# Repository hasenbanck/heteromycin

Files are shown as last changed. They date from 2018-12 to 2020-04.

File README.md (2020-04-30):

# Heteromycin - 3D printer board

Heteromycin is a 3D printer controller that aims to provide a full stack user
experience around Octoprint / Marlin using a custom designed board that
integrates a Raspberry Pi 3 or Zero W. It will also provide a solid, powerfull
hardware by utilizing quality components, a STM32 32bit MCU and powerfull
TMC5160 or TMC2160 driver (SD / SPI mode).

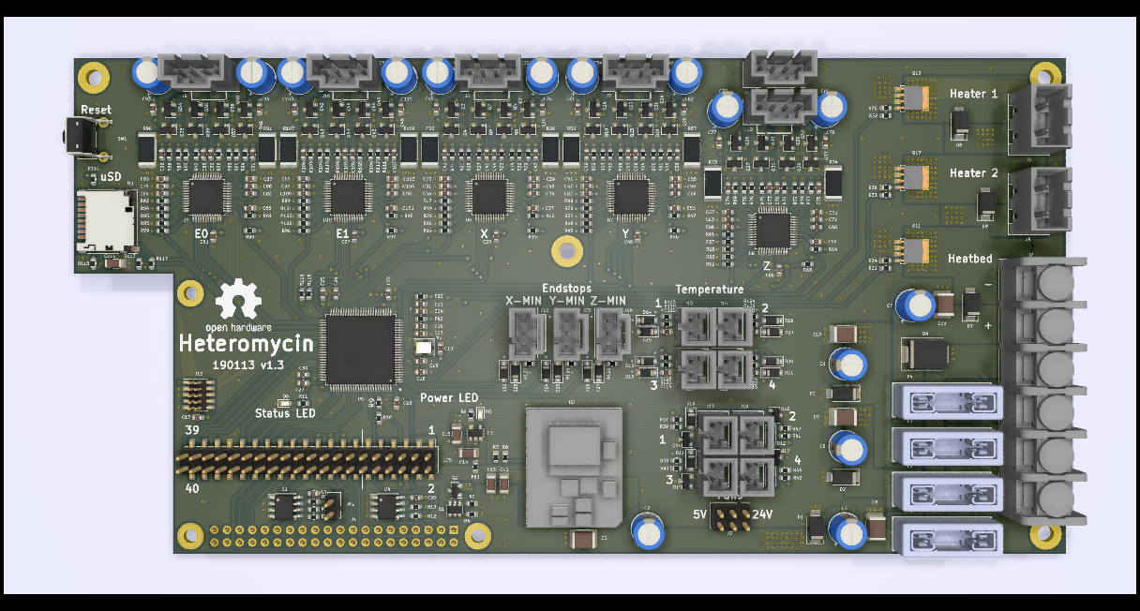
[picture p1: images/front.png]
heteromycin version 1.0


## Features

* 32bit STM32H743VI 400Mhz / 1024KiB RAM / 2MiB Flash MCU / 4 KiB EEPROM
* Integrated Raspberry Pi 3 / Zero W HAT connector as the main user interface
* Integrated DC/DC switching module for 5V / 3.3V power supply
* 5x TMC5160 or TMC2160 stepper driver with 8x external Power MOSFET each
* 3x high power MOSFET for heating (2x heater, 1x heatbed, 24V)
* 4x low power MOSFET for fans (5V or 24V)
* 40 pin external connector for STM32 and Pi GPIO pins
  * GPIO
  * PWM
  * UART
  * SPI
  * I2C
  * 3.3V / 5V / GND for external power consumption
* Micro SD Card for storing GCODE files (directa MCU access)
* Designed for a 24V power supply
* Automotive fuses
* Quality connectors
* Octoprint plugin for flashing the firmware of the board (STM32)

## Roadmap

* Hardware
  * [x] Describe the general functionality and select the main components
  * [x] Draw the schematics of the PCB
  * [x] Placement & routing of the PCB
  * [ ] Production of a development board
  * [ ] Testing the PCB
  * [ ] Repreat until hardware is finished
* Software
  * [x] Write arduino core board definition once first PCB design is finished
  * [ ] Write PIN file for Marlin
  * [ ] Test board (esp. the TMC*160 driver)
  * [ ] Octoprint plugin for firmware upgrade
  * [ ] STM32flash rewrite (fix I2C and add SPI, maybe rewrite in rust)
  * [ ] Create a script / image with Octoprint with the plugin / tools
  preinstalled
  * [ ] Documentation

## Alternative Parts

### Stepper driver

You can use both TMC5160 or TMC2160 as the stepper driver, since they both are
functionally / pin equal when used in SD / SPI-Mode.

It doesn't mater choosing one over the other, other than price and availability.

Fine tuning of the MOSFET driver may be necessary.

## License

The hardware is licensed under CERN OHL version 1.2.
The software is licensed under GNU GPL v3.

The files under PCB/packages3d are excluded from this license and are provided
under fair use terms for this open-source project.

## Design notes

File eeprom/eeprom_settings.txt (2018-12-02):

########################################################################
# EEPROM settings text file
#
# Edit this file for your particular board and run through eepmake tool,
# then use eepflash tool to write to attached HAT ID EEPROM
#
# Tools available:
#  eepmake   Parses EEPROM text file and creates binary .eep file
#  eepdump   Dumps a binary .eep file as human readable text (for debug)
#  eepflash  Write or read .eep binary image to/from HAT EEPROM
#
########################################################################

########################################################################
# Vendor info

# 128 bit UUID. If left at zero eepmake tool will auto-generate
# RFC 4122 compliant UUID
product_uuid ba184594-9e9b-4886-a79a-3c380cfe95e4

# 16 bit product id
product_id 0xFE10

# 16 bit product version
product_ver 0x0001

# ASCII vendor string  (max 255 characters)
vendor "Heteromycin development team"

# ASCII product string (max 255 characters)
product "3D printer controller Heteromycin"

########################################################################
# GPIO bank settings, set to nonzero to change from the default.
# NOTE these setting can only be set per BANK, uncommenting any of
# these will force the bank to use the custom setting.

# drive strength, 0=default, 1-8=2,4,6,8,10,12,14,16mA, 9-15=reserved
gpio_drive 0

# 0=default, 1=slew rate limiting, 2=no slew limiting, 3=reserved
gpio_slew 0

# 0=default, 1=hysteresis disabled, 2=hysteresis enabled, 3=reserved
gpio_hysteresis 0

# If board back-powers Pi via 5V GPIO header pins:
# 0 = board does not back-power
# 1 = board back-powers and can supply the Pi with a minimum of 1.3A
# 2 = board back-powers and can supply the Pi with a minimum of 2A
# 3 = reserved
# If back_power=2 then USB high current mode will be automatically
# enabled on the Pi
back_power 2 # Heteromycin can provide up to 8A on the 5V rail

########################################################################
# GPIO pins, uncomment for GPIOs used on board
# Options for FUNCTION: INPUT, OUTPUT, ALT0-ALT5
# Options for PULL: DEFAULT, UP, DOWN, NONE
# NB GPIO0 and GPIO1 are reserved for ID EEPROM so cannot be set

#         GPIO  FUNCTION  PULL
#         ----  --------  ----

#####
# We define GPIO pins at startup as INPUTS and user programms can later
# define the needed behavior, this way we boot in a known state and don't
# cause any unforseen resets or problems.
#####

setgpio  2     ALT0     DEFAULT # SDA
setgpio  3     ALT0     DEFAULT # SCL
setgpio  4     INPUT    NONE    # MCU BOOT Pin
setgpio  5     INPUT    NONE # GPIO
setgpio  6     INPUT    NONE # GPIO
setgpio  7     ALT0     DEFAULT # SS_0
setgpio  8     ALT0     DEFAULT # SS_1
setgpio  9     ALT0     DEFAULT # MISO
setgpio  10    ALT0     DEFAULT # MOSI
setgpio  11    ALT0     DEFAULT # SCLK
#setgpio  12    INPUT     DEFAULT
setgpio  13    INPUT    DEFAULT # GPIO
setgpio  14    ALT0     DEFAULT # TX
setgpio  15    ALT0     DEFAULT # RX
#setgpio  16    INPUT     DEFAULT
#setgpio  17    INPUT     DEFAULT
setgpio  18    INPUT    NONE # MCU nRESET Pin
setgpio  19    INPUT    NONE # GPIO
#setgpio  20    INPUT     DEFAULT
#setgpio  21    INPUT     DEFAULT
#setgpio  22    INPUT     DEFAULT
#setgpio  23    INPUT     DEFAULT
#setgpio  24    INPUT     DEFAULT
#setgpio  25    INPUT     DEFAULT
#setgpio  26    INPUT     DEFAULT
#setgpio  27    INPUT     DEFAULT

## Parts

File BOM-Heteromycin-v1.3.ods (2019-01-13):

Reference(s) | Value | Mft. Nr. | Digikey Nr. | Mouser Nr. | LCSC Nr. | Qty | Footprint | Note | Datasheet
C1, C16, C17, C18, C19, C22, C23, C24, C25, C26, C27, C29, C31, C33, C39, C40, C47, C49, C55, C56, C63, C65, C71, C72, C79, C81, C87, C88, C95, C97, C103, C104, C112, C113, C114, C115 | 100nF | C0603C104M5RACTU | C0603C104M5RACTU | 81-GCM188L81H104KA7D | C42998 | 36 | Capacitor_SMD:C_0603_1608Metric | Min. 35V | ~
C2, C4, C5, C6, C7, C32, C38, C48, C54, C64, C70, C80, C86, C96, C102 | 100uF | 860020573008 | 732-8942-1-ND | 710-860020573008 |  | 15 | Capacitor_SMD:CP_Elec_6.3x5.7 | Min. 35V
C3, C8, C9, C10, C11 | 100nF | VJ1812Y104KXBAT | 478-4009-1-ND | 77-VJ1812Y104KXBAT | C106148 | 5 | Capacitor_SMD:C_1812_4532Metric | Min. 35V
C12, C14 | 22uF | LMK316ABJ226KL-T | 1276-1771-2-ND | 963-LMK316ABJ226KL-T | C92818 | 2 | Capacitor_SMD:C_1206_3216Metric | Min. 6V | ~
C13 | 100nF | VJ1206Y104JXQCW1BC | 732-12245-1-ND | 77-VJ1206Y104JXQCBC | C313097 | 1 | Capacitor_SMD:C_1206_3216Metric | Min. 6V | ~
C15, C111 | 10uF | EMK316BJ106MD-T | 1276-2877-1-ND | 963-EMK316BJ106MD-T | C50691 | 2 | Capacitor_SMD:C_1206_3216Metric | Min. 6V | ~
C20, C21 | 1uF | 885012106022 | 1276-6524-1-ND | 710-885012106022 | C95843 | 2 | Capacitor_SMD:C_0603_1608Metric | Min. 6V | ~
C28, C30, C35, C36, C51, C52, C67, C68, C83, C84, C99, C100 | 2.2uF | CGB3B1X5R1C225M055AC | 587-4861-1-ND | 810-CGB3B1X5R1C225MC | C106832 | 12 | Capacitor_SMD:C_0603_1608Metric | Min. 16V | ~
C34, C50, C66, C82, C98 | 22nF | C0603C223K1RACTU | 399-3476-1-ND | 80-C0603C223K1R | C77443 | 5 | Capacitor_SMD:C_0603_1608Metric | Min. 100V | ~
C37, C45, C46, C53, C61, C62, C69, C77, C78, C85, C93, C94, C101, C109, C110 | 470nF | GMK107B7474KAHT | 445-172475-1-ND | 963-GMK107B7474KAHT | C296719 | 15 | Capacitor_SMD:C_0603_1608Metric | Min. 35V | ~
C41, C42, C43, C44, C57, C58, C59, C60, C73, C74, C75, C76, C89, C90, C91, C92, C105, C106, C107, C108 | 220nF | GMK107BJ224KAHT | 490-12546-1-ND | 963-GMK107BJ224KAHT | C123521 | 20 | Capacitor_SMD:C_0603_1608Metric | Min. 35V | ~
D1, D2, D3 | SMAJ28A | SMAJ28A-13-F | SMAJ28A-FDICT-ND | 621-SMAJ28A-13-F | C353458 | 3 | Diode_SMD:D_SMA |  | https://www.mouser.de/datasheet/2/240/Littelfuse_TVS_Diode_SMAJ_Datasheet.pdf-540740.pdf
D4 | S3A-13-F | S3A-13-F | S3A-FDITR-ND | 621-S3A-F | C264105 | 1 | Diode_SMD:D_SMC |  | https://www.mouser.de/datasheet/2/115/ds16005-37880.pdf
D5 | LTST-C194KGKT | LTST-C194KGKT | 160-1834-1-ND | 859-LTST-C194KGKT | C125098 | 1 | LED_SMD:LED_0603_1608Metric |  | ~
D6 | LTST-C194KSKT | LTST-C194KSKT | 160-1836-1-ND | LTST-C194KSKT | C84268 | 1 | LED_SMD:LED_0603_1608Metric |  | ~
D7, D8, D9 | SK310A-LTP | SK310A-LTP | SK310A-LTPMSCT-ND | 833-SK310A-LTP | C91474 | 3 | Diode_SMD:D_SMA |  | https://www.mouser.de/ProductDetail/Micro-Commercial-Components-MCC/SK310A-TP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
D10, D11, D12, D13, D14, D15, D16, D17, D18, D19, D20, D21, D22, D23, D24, D25, D26, D27 | BAT54GWJ | BAT54GWJ | 1727-7328-1-ND | 841-BAT54GWJ |  | 18 | Diode_SMD:D_SOD-123 |  | https://www.mouser.de/datasheet/2/916/BAT54GW-1318921.pdf
F1, F2, F3, F4 | 3557-2 | 3557-2 | 36-3557-2-ND | 534-3557-2 |  | 4 | heteromycin:KEYSTONE-FUSE-3557-2 |  | ~
FB1, FB2, FB3 | MPZ1608S221A | MPZ1608S221A | 445-1565-2-ND | 810-MPZ1608S221A | C76815 | 3 | Resistor_SMD:R_0603_1608Metric |  | https://www.mouser.de/datasheet/2/400/eads_commercial_power_mpz1608_en-923650.pdf
J1 | M20-7832046 | M20-7832046 | 952-2150-ND | 855-M20-7832046 |  | 1 | Connector_PinSocket_2.54mm:PinSocket_2x20_P2.54mm_Vertical
J2 | 4DB-P108-06 | 4DB-P108-06 | 4DB-P108-06 | 571-214376679 |  | 1 | heteromycin:4DB-P108-06 | Alternative: OSTYK42106030 | https://www.mouser.de/datasheet/2/418/NG_CD_2-1437667-4_N8-639207.pdf
J3, J4 | 039531-1002 | 039531-1002 | WM7837-ND | 538-39531-1002 |  | 2 | heteromycin:39531-1002 |  | ~
J5 | 68602-406HLF | 68602-406HLF | 609-4934-ND | 649-68602-406HLF | C124384 | 1 | Connector_PinHeader_2.54mm:PinHeader_2x03_P2.54mm_Vertical |  | ~
J6, J7, J8, J9, J10, J21 | 70543-0003 | 70543-0003 | WM4802-ND | 538-70543-0003 |  | 6 | heteromycin:70543-0003 |  | https://www.mouser.de/ProductDetail/Molex/70543-0003
J11 | DM3D-SF | DM3D-SF | HR1941CT-ND | 798-DM3D-SF |  | 1 | Connector_Card:microSD_HC_Hirose_DM3D-SF |  | https://www.hirose.com/product/en/download_file/key_name/DM3/category/Catalog/doc_file_id/49662/?item_id=195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
J12 | 20021121-00010C4LF | 20021121-00010C4LF | 609-3695-1-ND | 649-202112100010C4LF |  | 1 | Connector_PinHeader_1.27mm:PinHeader_2x05_P1.27mm_Vertical_SMD |  | https://www.mouser.de/datasheet/2/18/20021121-1362884.pdf
J13, J14, J15, J16, J17, J18, J19, J20 | 70543-0001 | 70543-0001 | WM4800-ND | 538-70543-0001 |  | 8 | heteromycin:70543-0001 |  | https://www.mouser.de/ProductDetail/Molex/50-57-9402
J22, J23, J24 | 70543-0002 | 70543-0002 | WM4801-ND | 538-70543-0002 |  | 3 | heteromycin:70543-0002 |  | ~
J25 | 95157-140LF | 95157-140LF | 609-2231-ND | 649-95157-140LF |  | 1 | Connector_PinHeader_2.54mm:PinHeader_2x20_P2.54mm_Vertical_SMD |  | ~
JP1 | Jumper_2_Open | M20-9990246 | 952-2262-ND | 855-M20-9990246 | C124375 | 1 | Connector_PinHeader_2.54mm:PinHeader_1x02_P2.54mm_Vertical |  | ~
Q1 | DMMT5401 | DMMT5401 | DMMT5401-FDICT-ND | DMMT5401-7-F | C154733 | 1 | Package_TO_SOT_SMD:SOT-23-6
Q2 | DMG2305UX | DMG2305UX | DMG2305UX-13DICT-ND | 621-DMG2305UX-7 | C144153 | 1 | Package_TO_SOT_SMD:SOT-23 |  | https://www.diodes.com/assets/Datasheets/DMG2305UX.pdf
Q3, Q4, Q5, Q6, Q7, Q8, Q9, Q10, Q14, Q15, Q16, Q17, Q18, Q19, Q20, Q21, Q22, Q23, Q24, Q25, Q26, Q27, Q28, Q29, Q30, Q31, Q32, Q33, Q34, Q35, Q36, Q37, Q38, Q39, Q40, Q41, Q42, Q43, Q44, Q45, Q46, Q47, Q48, Q49 | IRLML0030TRPbF | IRLML0030TRPbF | IRLML0030TRPBFCT-ND | 942-IRLML0030TRPBF | C67272 | 44 | Package_TO_SOT_SMD:SOT-23 |  | https://www.infineon.com/dgdl/irlml0030pbf.pdf?fileId=5546d462533600a401535664773825df
Q11, Q12, Q13 | PSMN1R2-30YLC,115 | PSMN1R2-30YLC,115 | 1727-5295-1-ND | 771-PSMN1R230YLC115 | C134469 | 3 | heteromycin:SOT-669_LFPAK_ThermalVias-1 | Alternatives: PSMN1R8-40YLC,115; PSMN1R3-30YL,115 PSMN1R5-30YLC | https://assets.nexperia.com/documents/data-sheet/PSMN1R2-30YLC.pdf
R1, R5, R14, R15, R45, R46, R62, R63, R79, R80, R96, R97, R113, R114, R115, R116, R117, R118 | 47k | CR0603-FX-4702ELF | CR0603-FX-4702ELFTR-ND | 652-CR0603FX-4702ELF | C279997 | 18 | Resistor_SMD:R_0603_1608Metric |  | ~
R2, R3 | 3.9K | RC0603FR-103K9L | 311-3.90KHRCT-ND | 603-RC0603FR-103K9L | C25997 | 2 | Resistor_SMD:R_0603_1608Metric
R4, R9 | 10k | AC0603FR-0710KL | P10.0KHCT-ND | 603-AC0603FR-0710KL | C99198 | 2 | Resistor_SMD:R_0603_1608Metric |  | ~
R6 | 20k | RC0603FR-1020KL | YAG3577CT-ND | 603-RC0603FR-1020KL | C118368 | 1 | Resistor_SMD:R_0603_1608Metric |  | ~
R7 | 15k | RC0603FR-0715KL | 311-15.0KHRCT-ND | 603-RC0603FR-0715KL | C25581 | 1 | Resistor_SMD:R_0603_1608Metric |  | ~
R8, R11, R127, R128, R129 | 1k | RC0603JR-7W1KL | YAG2323CT-ND | 603-RC0603JR-7W1KL | C25585 | 5 | Resistor_SMD:R_0603_1608Metric |  | ~
R12, R13, R119, R120, R121, R122, R123, R124, R125, R126 | 4.7k | AC0603JR-074K7L | YAG3676CT-ND | 603-AC0603JR-074K7L | C25999 | 10 | Resistor_SMD:R_0603_1608Metric |  | ~
R16, R47, R64, R81, R98 | 2.2 | CRCW06032R20FKEA | 541-2.20SCT-ND | 71-CRCW0603-2.2-E3 | C25226 | 5 | Resistor_SMD:R_0603_1608Metric | Can also be 3.3 Ohm | ~
R17, R18, R19, R20, R48, R49, R50, R51, R65, R66, R67, R68, R82, R83, R84, R85, R99, R100, R101, R102 | 47 | RC0603FR-1047RL | A129672CT-ND | 603-RC0603FR-1047RL | C114623 | 20 | Resistor_SMD:R_0603_1608Metric |  | ~
R21, R22, R23, R24, R27, R28, R29, R30, R52, R53, R54, R55, R58, R59, R60, R61, R69, R70, R71, R72, R75, R76, R77, R78, R86, R87, R88, R89, R92, R93, R94, R95, R103, R104, R105, R106, R109, R110, R111, R112 | 10 | SFR03EZPF10R0 | RC0603FR-0710RL | 755-SFR03EZPF10R0 | C304686 | 40 | Resistor_SMD:R_0603_1608Metric |  | ~
R25, R26, R56, R57, R73, R74, R90, R91, R107, R108 | 0.1 | PE2512FKE070R1L | YAG2159CT-ND | 603-PE2512FKE070R1L | C159168 | 10 | Resistor_SMD:R_2512_6332Metric | 0.5 or 1W
R31, R32, R33, R37, R38, R41, R42 | 100 | RC0603FR-7W100RL | RMCF0603FG100RTR-ND | 603-RC0603FR-7W100RL | C25201 | 7 | Resistor_SMD:R_0603_1608Metric |  | ~
R10, R34, R35, R36, R39, R40, R43, R44 | 100k | CRCW0603100KFKEAC | 541-3950-1-ND | 71-CRCW0603100KFKEAC | C103211 | 8 | Resistor_SMD:R_0603_1608Metric |  | ~
SW1 | PTS645VL39-2 | PTS645VL392LFS | CKN9103-ND | 611-PTS645VL392 | C221891 | 1 | Button_Switch_THT:SW_Tactile_SPST_Angled_PTS645Vx39-2LFS |  | https://www.mouser.de/datasheet/2/60/-1131575.pdf
U1, U4 | CAT24C32 | CAT24C32WI-GT3 | CAT24C32WI-GT3CT-ND | 698-CAT24C32WI-GT3 | C81193 | 2 | Package_SO:SOIC-8_3.9x4.9mm_P1.27mm
U2 | I3A4W008A033V-001-R | I3A4W008A033V-001-R | 285-2720-ND | 967-I3A4W008A033V01R |  | 1 | heteromycin:i3A |  | https://www.us.tdk-lambda.com/ftp/specs/i3a_full_datasheet.pdf
U3 | AP7365-33WG-7 | AP7365-33WG-7 | AP7365-33WG-7DICT-ND | 621-AP7365-33WG-7 | C150742 | 1 | Package_TO_SOT_SMD:SOT-23-5 |  | https://www.mouser.de/datasheet/2/115/AP7365-86154.pdf
U5 | STM32H743VI | STM32H743VI | 497-17720-ND | 511-STM32H743VIT6 |  | 1 | heteromycin:TQFP-100_14x14mm_P0.5mm |  | https://www.st.com/en/microcontrollers/stm32h743vi.html
U6, U7, U8, U9, U10 | TMC2160-TA | TMC2160-TA | TMC2160-TA | - |  | 5 | heteromycin:TQFP-48-1EP_7x7mm_P0.5mm_EP5x5mm_ThermalVias | Not available at Mouser | https://www.trinamic.com/fileadmin/assets/Products/ICs_Documents/TMC5160_Datasheet_V1.01.pdf
X1 | ECS-TXO-3225-250-TR | ECS-TXO-3225-250-TR | XC2062CT-ND | 520-TXO-3225-25.0T |  | 1 | heteromycin:ECS-TXO-3225 |  | https://www.ecsxtal.com/store/pdf/ECS-TXO-3225.pdf
Jumper | Jumper | M7581-46 | S9337-ND | 855-M7581-46 |  | 3

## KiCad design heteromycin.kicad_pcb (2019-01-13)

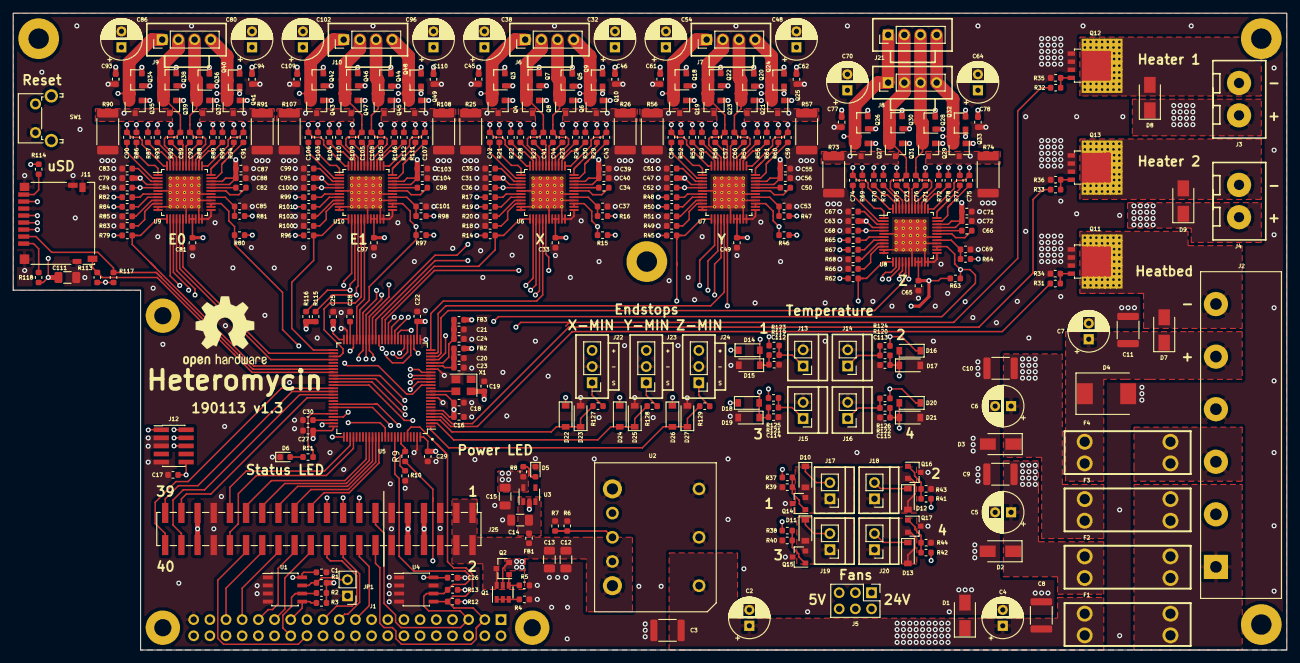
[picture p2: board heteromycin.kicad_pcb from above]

Board: 4 copper layers, 200.0 x 100.0 mm, 373 parts (1 on the bottom side), 293 nets.

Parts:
C1, C16, C17, C18, C19, C22, C23, C24, C25, C26, C27, C29, C31, C33, C39, C40, C47, C49, C55, C56, C63, C65, C71, C72, C79, C81, C87, C88, C95, C97, C103, C104, C112, C113, C114, C115: 100nF; C_0603_1608Metric
C2, C4, C5, C6, C7, C32, C38, C48, C54, C64, C70, C80, C86, C96, C102: 100uF; CP_Radial_D6.3mm_P2.50mm
C3, C8, C9, C10, C11: 100nF; C_1812_4532Metric
C12, C14: 22uF; C_1206_3216Metric
C13: 100nF; C_1206_3216Metric
C15, C111: 10uF; C_1206_3216Metric
C20, C21: 1uF; C_0603_1608Metric
C28, C30, C35, C36, C51, C52, C67, C68, C83, C84, C99, C100: 2.2uF; C_0603_1608Metric
C34, C50, C66, C82, C98: 22nF; C_0603_1608Metric
C37, C45, C46, C53, C61, C62, C69, C77, C78, C85, C93, C94, C101, C109, C110: 470nF; C_0603_1608Metric
C41, C42, C43, C44, C57, C58, C59, C60, C73, C74, C75, C76, C89, C90, C91, C92, C105, C106, C107, C108: 220nF; C_0603_1608Metric
D1, D2, D3: SMAJ28A; D_SMA
D4: S3A-13-F; D_SMC
D5: LTST-C194KGKT; LED_0603_1608Metric
D6: LTST-C194KSKT; LED_0603_1608Metric
D7, D8, D9: SK310A-LTP; D_SMA
D10, D11, D12, D13, D14, D15, D16, D17, D18, D19, D20, D21, D22, D23, D24, D25, D26, D27: BAT54GWJ; D_SOD-123
F1, F2, F3, F4: 3557-2; KEYSTONE-FUSE-3557-2
FB1, FB2, FB3: MPZ1608S221A; R_0603_1608Metric
H1, H2, H5: MountingHole_2.7mm_M2.5_Pad
H3, H4, H6, H7: MountingHole_3.2mm_M3_Pad
J1: M20-7832046; PinSocket_2x20_P2.54mm_Vertical
J2: 4DB-P108-06
J3, J4: 39531-1002
J5: Conn_02x03_Counter_Clockwise; PinHeader_2x03_P2.54mm_Vertical
J6, J7, J8, J9, J10, J21: 70543-0003
J11: DM3D-SF; microSD_HC_Hirose_DM3D-SF
J12: 20021121-00010C4LF; PinHeader_2x05_P1.27mm_Vertical_SMD
J13, J14, J15, J16, J17, J18, J19, J20: 70543-0001
J22, J23, J24: 70543-0002
J25: Conn_02x20_Odd_Even; PinHeader_2x20_P2.54mm_Vertical_SMD
JP1: Jumper_2_Open; PinHeader_1x02_P2.54mm_Vertical
LOGO1: Logo_Open_Hardware_Large; OSHW-Logo2_14.6x12mm_SilkScreen
Q1: DMMT5401; SOT-23-6
Q2: DMG2305UX; SOT-23
Q3, Q4, Q5, Q6, Q7, Q8, Q9, Q10, Q14, Q15, Q16, Q17, Q18, Q19, Q20, Q21, Q22, Q23, Q24, Q25, Q26, Q27, Q28, Q29, Q30, Q31, Q32, Q33, Q34, Q35, Q36, Q37, Q38, Q39, Q40, Q41, Q42, Q43, Q44, Q45, Q46, Q47, Q48, Q49: IRLML0030TRPbF; SOT-23
Q11, Q12, Q13: PSMN1R2-30YLC,115; SOT-669_LFPAK_ThermalVias-1
R1, R5, R14, R15, R45, R46, R62, R63, R79, R80, R96, R97, R113, R114, R115, R116, R117, R118: 47k; R_0603_1608Metric
R2, R3: 3.9K; R_0603_1608Metric
R4, R9: 10k; R_0603_1608Metric
R6: 20k; R_0603_1608Metric
R7: 15k; R_0603_1608Metric
R8, R11, R127, R128, R129: 1k; R_0603_1608Metric
R10, R34, R35, R36, R39, R40, R43, R44: 100k; R_0603_1608Metric
R12, R13, R119, R120, R121, R122, R123, R124, R125, R126: 4.7k; R_0603_1608Metric
R16, R47, R64, R81, R98: 2.2; R_0603_1608Metric
R17, R18, R19, R20, R48, R49, R50, R51, R65, R66, R67, R68, R82, R83, R84, R85, R99, R100, R101, R102: 47; R_0603_1608Metric
R21, R22, R23, R24, R27, R28, R29, R30, R52, R53, R54, R55, R58, R59, R60, R61, R69, R70, R71, R72, R75, R76, R77, R78, R86, R87, R88, R89, R92, R93, R94, R95, R103, R104, R105, R106, R109, R110, R111, R112: 10; R_0603_1608Metric
R25, R26, R56, R57, R73, R74, R90, R91, R107, R108: 0.1; R_2512_6332Metric
R31, R32, R33, R37, R38, R41, R42: 100; R_0603_1608Metric
SW1: PTS645VL39-2; SW_Tactile_SPST_Angled_PTS645Vx39-2LFS
U1, U4: CAT24C32; SOIC-8_3.9x4.9mm_P1.27mm
U2: i3A
U3: AP7365-33WG-7; SOT-23-5
U5: STM32H743VI; TQFP-100_14x14mm_P0.5mm
U6, U7, U8, U9, U10: TMC2160-TA; TQFP-48-1EP_7x7mm_P0.5mm_EP5x5mm_ThermalVias
X1: ECS-TXO-3225-250-TR; ECS-TXO-3225

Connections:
/Connectors/MCU_MISO: J11.7, J25.17, R115.1, U5.43, U6.16, U7.16, U8.16, U9.16, U10.16
/Connectors/MCU_MOSI: J11.3, J25.19, R116.1, U5.44, U6.15, U7.15, U8.15, U9.15, U10.15
/Connectors/MCU_SCK: J11.5, J25.15, U5.42, U6.14, U7.14, U8.14, U9.14, U10.14
/Connectors/PI_SCK: J1.23, J25.20, U5.29
/Connectors/PI_SS1: J1.26, J25.30
/Connectors/PWM_EXT1: J25.37, U5.66
/Connectors/PWM_EXT2: J25.38, U5.65
/Connectors/PWM_EXT3: J25.39, U5.64
/Connectors/PWM_EXT4: J25.40, U5.63
/Connectors/RX: J25.32, U5.79
/Connectors/SCL: J1.5, J25.13, R13.1, U4.6, U5.92
/Connectors/SDA: J1.3, J25.14, R12.1, U4.5, U5.96
/Connectors/SWCLK: J12.4, U5.76
/Connectors/SWDIO: J12.2, U5.72
/Connectors/SWO: J12.6, U5.89
/Connectors/TEMP1: C112.1, D14.2, D15.1, R119.2, U5.18
/Connectors/TEMP2: C113.1, D16.2, D17.1, R120.2, U5.17
/Connectors/TEMP3: C114.1, D18.2, D19.1, R121.2, U5.16
/Connectors/TEMP4: C115.1, D20.2, D21.1, R122.2, U5.15
/Connectors/TX: J25.31, U5.78
/Connectors/X_MIN: D22.2, D23.1, R127.2, U5.3
/Connectors/Y_MIN: D24.2, D25.1, R128.2, U5.2
/Connectors/Z_MIN: D26.2, D27.1, R129.2, U5.1
/Connectors/nRESET: C17.2, J1.12, J12.10, SW1.2, U5.14
/MCU/BOOT: J1.7, R9.1
/MCU/BOOTpin: R9.2, R10.2, U5.94
/MCU/CLK: U5.12, X1.3
/MCU/D1: J25.21, U5.87
/MCU/D2: J25.23, U5.86
/MCU/D3: J25.25, U5.85
/MCU/D4: J25.27, U5.84
/MCU/D5: J25.29, U5.83
/MCU/MCU_SS: J1.24, U5.28
/MCU/PWM_BED: R31.2, U5.4
/MCU/PWM_FAN1: R37.2, U5.59
/MCU/PWM_FAN2: R41.2, U5.60
/MCU/PWM_FAN3: R38.2, U5.61
/MCU/PWM_FAN4: R42.2, U5.62
/MCU/PWM_HEAT1: R32.2, U5.22
/MCU/PWM_HEAT2: R33.2, U5.5
/MCU/SD_DETECT: J11.10, R113.1, U5.58
/MCU/STATUS_LED: R11.1, U5.71
/MCU/VCAP1: C28.2, U5.48
/MCU/VCAP2: C30.2, U5.73
/MCU/VDDA: C21.1, C24.1, FB3.1, U5.21
/MCU/VREF+: C20.2, C23.2, FB2.1, U5.20
/Raspberry Pi Connector/D1: J1.29, J25.22
/Raspberry Pi Connector/D2: J1.31, J25.24
/Raspberry Pi Connector/D3: J1.33, J25.26
/Raspberry Pi Connector/D4: J1.35, J25.28
/Raspberry Pi Connector/ID_SC_EEPROM: J1.28, R2.2, U1.6
/Raspberry Pi Connector/ID_SD_EEPROM: J1.27, R3.2, U1.5
/Raspberry Pi Connector/MISO: J1.21, J25.18, U5.30
/Raspberry Pi Connector/MOSI: J1.19, J25.16, U5.31
/Raspberry Pi Connector/RX: J1.10, U5.68
/Raspberry Pi Connector/TX: J1.8, U5.69
/Raspberry Pi Connector/VDD5V_HAT: J1.2, J1.4, Q1.5, Q2.2
/SD Card Reader/SS: J11.2, R117.1, U5.57
/Steper Motor Y/5VOUT: C52.1, R47.2, U7.5
/Steper Motor Y/12VOUT: C51.1, U7.3
/Steper Motor Y/BMA1: C60.2, J7.3, Q20.3, Q21.2, U7.40
/Steper Motor Y/BMA2: C59.2, J7.4, Q24.3, Q25.2, U7.37
/Steper Motor Y/BMB1: C58.2, J7.1, Q18.3, Q19.2, U7.48
/Steper Motor Y/BMB2: C57.2, J7.2, Q22.3, Q23.2, U7.45
/Steper Motor Y/CA1: C60.1, U7.42
/Steper Motor Y/CA2: C59.1, U7.35
/Steper Motor Y/CB1: C58.1, U7.2
/Steper Motor Y/CB2: C57.1, U7.43
/Steper Motor Y/CPI: C50.1, U7.32
/Steper Motor Y/CPO: C50.2, U7.31
/Steper Motor Y/DIAG: R46.1, U5.40, U7.26, U7.27
/Steper Motor Y/DIR: U5.35, U7.18
/Steper Motor Y/HA1: R54.1, U7.41
/Steper Motor Y/HA2: R60.2, U7.36
/Steper Motor Y/HB1: R52.1, U7.1
/Steper Motor Y/HB2: R58.2, U7.44
/Steper Motor Y/LA1: R55.1, U7.39
/Steper Motor Y/LA2: R61.2, U7.38
/Steper Motor Y/LB1: R53.1, U7.47
/Steper Motor Y/LB2: R59.2, U7.46
/Steper Motor Y/SRAH: R50.1, U7.8
/Steper Motor Y/SRAL: R51.1, U7.9
/Steper Motor Y/SRBH: R48.2, U7.7
/Steper Motor Y/SRBL: R49.1, U7.10
/Steper Motor Y/SS: R45.1, U5.36, U7.13
/Steper Motor Y/STEP: U5.24, U7.17
/Steper Motor Y/VCC: C53.1, R47.1, U7.29
/Stepper Motor E0/5VOUT: C84.1, R81.2, U9.5
/Stepper Motor E0/12VOUT: C83.1, U9.3
/Stepper Motor E0/BMA1: C92.2, J9.3, Q36.3, Q37.2, U9.40
/Stepper Motor E0/BMA2: C91.2, J9.4, Q40.3, Q41.2, U9.37
/Stepper Motor E0/BMB1: C90.2, J9.1, Q34.3, Q35.2, U9.48
/Stepper Motor E0/BMB2: C89.2, J9.2, Q38.3, Q39.2, U9.45
/Stepper Motor E0/CA1: C92.1, U9.42
/Stepper Motor E0/CA2: C91.1, U9.35
/Stepper Motor E0/CB1: C90.1, U9.2
/Stepper Motor E0/CB2: C89.1, U9.43
/Stepper Motor E0/CPI: C82.1, U9.32
/Stepper Motor E0/CPO: C82.2, U9.31
/Stepper Motor E0/DIAG: R80.1, U5.47, U9.26, U9.27
/Stepper Motor E0/DIR: U5.52, U9.18
/Stepper Motor E0/HA1: R88.1, U9.41
/Stepper Motor E0/HA2: R94.2, U9.36
/Stepper Motor E0/HB1: R86.1, U9.1
/Stepper Motor E0/HB2: R92.2, U9.44
/Stepper Motor E0/LA1: R89.1, U9.39
/Stepper Motor E0/LA2: R95.2, U9.38
/Stepper Motor E0/LB1: R87.1, U9.47
/Stepper Motor E0/LB2: R93.2, U9.46
/Stepper Motor E0/SRAH: R84.1, U9.8
/Stepper Motor E0/SRAL: R85.1, U9.9
/Stepper Motor E0/SRBH: R82.2, U9.7
/Stepper Motor E0/SRBL: R83.1, U9.10
/Stepper Motor E0/SS: R79.1, U5.56, U9.13
/Stepper Motor E0/STEP: U5.54, U9.17
/Stepper Motor E0/VCC: C85.1, R81.1, U9.29
/Stepper Motor E1/5VOUT: C100.1, R98.2, U10.5
/Stepper Motor E1/12VOUT: C99.1, U10.3
/Stepper Motor E1/BMA1: C108.2, J10.3, Q44.3, Q45.2, U10.40
/Stepper Motor E1/BMA2: C107.2, J10.4, Q48.3, Q49.2, U10.37
/Stepper Motor E1/BMB1: C106.2, J10.1, Q42.3, Q43.2, U10.48
/Stepper Motor E1/BMB2: C105.2, J10.2, Q46.3, Q47.2, U10.45
/Stepper Motor E1/CA1: C108.1, U10.42
/Stepper Motor E1/CA2: C107.1, U10.35
/Stepper Motor E1/CB1: C106.1, U10.2
/Stepper Motor E1/CB2: C105.1, U10.43
/Stepper Motor E1/CPI: C98.1, U10.32
/Stepper Motor E1/CPO: C98.2, U10.31
/Stepper Motor E1/DIAG: R97.1, U5.45, U10.26, U10.27
/Stepper Motor E1/DIR: U5.46, U10.18
/Stepper Motor E1/HA1: R105.1, U10.41
/Stepper Motor E1/HA2: R111.2, U10.36
/Stepper Motor E1/HB1: R103.1, U10.1
/Stepper Motor E1/HB2: R109.2, U10.44
/Stepper Motor E1/LA1: R106.1, U10.39
/Stepper Motor E1/LA2: R112.2, U10.38
/Stepper Motor E1/LB1: R104.1, U10.47
/Stepper Motor E1/LB2: R110.2, U10.46
/Stepper Motor E1/SRAH: R101.1, U10.8
/Stepper Motor E1/SRAL: R102.1, U10.9
/Stepper Motor E1/SRBH: R99.2, U10.7
/Stepper Motor E1/SRBL: R100.1, U10.10
/Stepper Motor E1/SS: R96.1, U5.51, U10.13
/Stepper Motor E1/STEP: U5.53, U10.17
/Stepper Motor E1/VCC: C101.1, R98.1, U10.29
/Stepper Motor X/5VOUT: C36.1, R16.2, U6.5
/Stepper Motor X/12VOUT: C35.1, U6.3
/Stepper Motor X/BMA1: C44.2, J6.3, Q5.3, Q6.2, U6.40
/Stepper Motor X/BMA2: C43.2, J6.4, Q9.3, Q10.2, U6.37
/Stepper Motor X/BMB1: C42.2, J6.1, Q3.3, Q4.2, U6.48
/Stepper Motor X/BMB2: C41.2, J6.2, Q7.3, Q8.2, U6.45
/Stepper Motor X/CA1: C44.1, U6.42
/Stepper Motor X/CA2: C43.1, U6.35
/Stepper Motor X/CB1: C42.1, U6.2
/Stepper Motor X/CB2: C41.1, U6.43
/Stepper Motor X/CPI: C34.1, U6.32
/Stepper Motor X/CPO: C34.2, U6.31
/Stepper Motor X/DIAG: R15.1, U5.41, U6.26, U6.27
/Stepper Motor X/DIR: U5.37, U6.18
/Stepper Motor X/HA1: R23.1, U6.41
/Stepper Motor X/HA2: R29.2, U6.36
/Stepper Motor X/HB1: R21.1, U6.1
/Stepper Motor X/HB2: R27.2, U6.44
/Stepper Motor X/LA1: R24.1, U6.39
/Stepper Motor X/LA2: R30.2, U6.38
/Stepper Motor X/LB1: R22.1, U6.47
/Stepper Motor X/LB2: R28.2, U6.46
/Stepper Motor X/SRAH: R19.1, U6.8
/Stepper Motor X/SRAL: R20.1, U6.9
/Stepper Motor X/SRBH: R17.2, U6.7
/Stepper Motor X/SRBL: R18.1, U6.10
/Stepper Motor X/SS: R14.1, U5.38, U6.13
/Stepper Motor X/STEP: U5.25, U6.17
/Stepper Motor X/VCC: C37.1, R16.1, U6.29
/Stepper Motor Z/5VOUT: C68.1, R64.2, U8.5
/Stepper Motor Z/12VOUT: C67.1, U8.3
/Stepper Motor Z/BMA1: C76.2, J8.3, J21.3, Q28.3, Q29.2, U8.40
/Stepper Motor Z/BMA2: C75.2, J8.4, J21.4, Q32.3, Q33.2, U8.37
/Stepper Motor Z/BMB1: C74.2, J8.1, J21.1, Q26.3, Q27.2, U8.48
/Stepper Motor Z/BMB2: C73.2, J8.2, J21.2, Q30.3, Q31.2, U8.45
/Stepper Motor Z/CA1: C76.1, U8.42
/Stepper Motor Z/CA2: C75.1, U8.35
/Stepper Motor Z/CB1: C74.1, U8.2
/Stepper Motor Z/CB2: C73.1, U8.43
/Stepper Motor Z/CPI: C66.1, U8.32
/Stepper Motor Z/CPO: C66.2, U8.31
/Stepper Motor Z/DIAG: R63.1, U5.39, U8.26, U8.27
/Stepper Motor Z/DIR: U5.33, U8.18
/Stepper Motor Z/HA1: R71.1, U8.41
/Stepper Motor Z/HA2: R77.2, U8.36
/Stepper Motor Z/HB1: R69.1, U8.1
/Stepper Motor Z/HB2: R75.2, U8.44
/Stepper Motor Z/LA1: R72.1, U8.39
/Stepper Motor Z/LA2: R78.2, U8.38
/Stepper Motor Z/LB1: R70.1, U8.47
/Stepper Motor Z/LB2: R76.2, U8.46
/Stepper Motor Z/SRAH: R67.1, U8.8
/Stepper Motor Z/SRAL: R68.1, U8.9
/Stepper Motor Z/SRBH: R65.2, U8.7
/Stepper Motor Z/SRBL: R66.1, U8.10
/Stepper Motor Z/SS: R62.1, U5.34, U8.13
/Stepper Motor Z/STEP: U5.23, U8.17
/Stepper Motor Z/VCC: C69.1, R64.1, U8.29
BED_OUT: D7.2, J2.6, Q11.5
FAN1_OUT: D10.2, J17.1, Q14.2
FAN2_OUT: D12.2, J18.1, Q16.2
FAN3_OUT: D11.2, J19.1, Q15.2
FAN4_OUT: D13.2, J20.1, Q17.2
GND: C1.2, C2.2, C3.2, C4.2, C5.2, C6.2, C7.2, C8.2, C9.2, C10.2, C11.2, C12.2, C13.2, C14.2, C15.2, C16.2, C17.1, C18.2, C19.2, C20.1, C21.2, C22.2, C23.1, C24.2, C25.2, C26.2, C27.2, C28.1, C29.2, C30.1, C31.2, C32.2, C33.2, C35.2, C36.2, C37.2, C38.2, C39.2, C40.2, C45.2, C46.2, C47.2, C48.2, C49.2, C51.2, C52.2, C53.2, C54.2, C55.2, C56.2, C61.2, C62.2, C63.2, C64.2, C65.2, C67.2, C68.2, C69.2, C70.2, C71.2, C72.2, C77.2, C78.2, C79.2, C80.2, C81.2, C83.2, C84.2, C85.2, C86.2, C87.2, C88.2, C93.2, C94.2, C95.2, C96.2, C97.2, C99.2, C100.2, C101.2, C102.2, C103.2, C104.2, C109.2, C110.2, C111.2, C112.2, C113.2, C114.2, C115.2, D1.2, D2.2, D3.2, D4.2, D5.1, D6.1, D15.2, D17.2, D19.2, D21.2, D23.2, D25.2, D27.2, J1.6, J1.9, J1.14, J1.20, J1.25, J1.30, J1.34, J1.39, J2.2, J2.4, J11.6, J11.9, J11.11, J12.3, J12.5, J12.9, J13.2, J14.2, J15.2, J16.2, J22.2, J23.2, J24.2, J25.5, J25.6, J25.11, J25.12, J25.33, J25.34, JP1.1, Q11.1, Q11.2, Q11.3, Q12.1, Q12.2, Q12.3, Q13.1, Q13.2, Q13.3, Q14.3, Q15.3, Q16.3, Q17.3, R4.2, R5.2, R6.2, R7.2, R10.1, R18.2, R20.2, R25.1, R26.1, R34.1, R35.1, R36.1, R39.1, R40.1, R43.1, R44.1, R49.2, R51.2, R56.1, R57.1, R66.2, R68.2, R73.1, R74.1, R83.2, R85.2, R90.1, R91.1, R100.2, R102.2, R107.1, R108.1, SW1.1, U1.1, U1.2, U1.3, U1.4, U2.2, U2.3, U2.4, U3.2, U4.1, U4.2, U4.3, U4.4, U4.7, U5.10, U5.19, U5.26, U5.49, U5.74, U5.99, U6.6, U6.11, U6.12, U6.19, U6.23, U6.24, U6.25, U6.28, U6.30, U6.49, U7.6, U7.11, U7.12, U7.19, U7.23, U7.24, U7.25, U7.28, U7.30, U7.49, U8.6, U8.11, U8.12, U8.19, U8.23, U8.24, U8.25, U8.28, U8.30, U8.49, U9.6, U9.11, U9.12, U9.19, U9.23, U9.24, U9.25, U9.28, U9.30, U9.49, U10.6, U10.11, U10.12, U10.19, U10.23, U10.24, U10.25, U10.28, U10.30, U10.49, X1.2
HEAT1_OUT: D8.2, J3.1, Q12.5
HEAT2_OUT: D9.2, J4.1, Q13.5
unnamed: C14.1, FB1.1, U3.1, U3.3
unnamed: D5.2, R8.2
unnamed: D6.2, R11.2
unnamed: F1.2, F2.2, F3.2, J2.1
unnamed: F4.2, J2.3
unnamed: J11.1, R118.1
unnamed: J11.8, R114.1
unnamed: J13.1, R119.1, R123.2
unnamed: J14.1, R120.1, R124.2
unnamed: J15.1, R121.1, R125.2
unnamed: J16.1, R122.1, R126.2
unnamed: J22.1, R127.1
unnamed: J23.1, R128.1
unnamed: J24.1, R129.1
unnamed: JP1.2, R1.1, U1.7
unnamed: Q1.1, Q1.2, Q1.3, R4.1
unnamed: Q1.4, Q2.1, R5.1
unnamed: Q3.1, R21.2
unnamed: Q4.1, R22.2
unnamed: Q4.3, Q8.3, R17.1, R25.2
unnamed: Q5.1, R23.2
unnamed: Q6.1, R24.2
unnamed: Q7.1, R27.1
unnamed: Q8.1, R28.1
unnamed: Q9.1, R29.1
unnamed: Q10.1, R30.1
unnamed: Q6.3, Q10.3, R19.2, R26.2
unnamed: Q11.4, R31.1, R34.2
unnamed: Q12.4, R32.1, R35.2
unnamed: Q13.4, R33.1, R36.2
unnamed: Q14.1, R37.1, R39.2
unnamed: Q15.1, R38.1, R40.2
unnamed: Q16.1, R41.1, R43.2
unnamed: Q17.1, R42.1, R44.2
unnamed: Q18.1, R52.2
unnamed: Q19.1, R53.2
unnamed: Q19.3, Q23.3, R48.1, R56.2
unnamed: Q20.1, R54.2
unnamed: Q21.1, R55.2
unnamed: Q21.3, Q25.3, R50.2, R57.2
unnamed: Q22.1, R58.1
unnamed: Q23.1, R59.1
unnamed: Q24.1, R60.1
unnamed: Q25.1, R61.1
unnamed: Q26.1, R69.2
unnamed: Q27.1, R70.2
unnamed: Q27.3, Q31.3, R65.1, R73.2
unnamed: Q28.1, R71.2
unnamed: Q29.1, R72.2
unnamed: Q29.3, Q33.3, R67.2, R74.2
unnamed: Q30.1, R75.1
unnamed: Q31.1, R76.1
unnamed: Q32.1, R77.1
unnamed: Q33.1, R78.1
unnamed: Q34.1, R86.2
unnamed: Q35.1, R87.2
unnamed: Q35.3, Q39.3, R82.1, R90.2
unnamed: Q36.1, R88.2
unnamed: Q37.1, R89.2
unnamed: Q37.3, Q41.3, R84.2, R91.2
unnamed: Q38.1, R92.1
unnamed: Q39.1, R93.1
unnamed: Q40.1, R94.1
unnamed: Q41.1, R95.1
unnamed: Q42.1, R103.2
unnamed: Q43.1, R104.2
unnamed: Q43.3, Q47.3, R99.1, R107.2
unnamed: Q44.1, R105.2
unnamed: Q45.1, R106.2
unnamed: Q45.3, Q49.3, R101.2, R108.2
unnamed: Q46.1, R109.1
unnamed: Q47.1, R110.1
unnamed: Q48.1, R111.1
unnamed: Q49.1, R112.1
unnamed: R6.1, R7.1, U2.6
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

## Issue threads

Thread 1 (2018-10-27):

Sense Resistor Value

kAdonis, 2018-10-27:
Wow, this project looks awesome!

I am a big fan of the TMC5160 and I am looking forward to see your board running
are you sure about the sense resistor value? I think 0,075 Ohm is a bit low
The advantage is the high motor current of 3,1A, but it could lead to problems for smaller motors

The current is scaled down by Globalscaler and CS, the datasheet recommends CS ≥16 and Globalscaler > 128

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

which means a minimum (recommended) RMS motor current of  820 mA
Most Nema17 motors in 3d Printers need an I rms 600-1000 mA so I would suggest using
at least 0,1 or 0,12 Ohm sense resistors.

I see you live in Hamburg, have you talked to Trinamic about your Project?

I am using TMC5160BOB with 0.22 Ohm sense resistors in standalone mode for X and Y in my printer,
running fine (in Stealthchop) at 720mA rms with 1,5A motors

hasenbanck, 2018-10-27:
Thank you for the feedback! The premise when designing this board was: "Let's make it stupid powerful". In the first iteration I want to test how the board works with totally insane values (3,1 A for 3D printer that use 99% NEMA17 stepper with a max current of 1.2 / 1.5 A ....). That's why I settled with 0.075Ohm sense resistors.

I will test the current setup and want to see how well the stepper driver scale down with GS/CS outside of the recommended values. If those values turn our problematic, I will gladly adjust those values. Luckily the sense resistors are easily adjusted in future versions and can also easily be changed / configured by the end user (if he has a (hot air) solder iron).

Speaking about "stupid powerful": I originally wanted to use the STM32H7 (400 MHz) of the new value line with external flash memory. But sadly their HAL isn't up to standard yet and the Arduino Core doesn't support them yet.

I haven't contacted Trinamic yet. Don't know if this project would be valuable for them or not.

hasenbanck, 2018-11-24:
The next design (v1.2) will have sense resistor values of 0.1 Ohm. This should act as a more sensible default value and allows for a maximum current of 2.3A.

Closed 2018-12-02.

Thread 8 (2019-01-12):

TMC2160/TMC5160 Charge pump capacitors

G-Pereira, 2019-01-12:
I've noticed the capacitors used in the charge pump terminals of the drivers were rated for 50V while the datasheet recommends 100V.
Datasheet page 13 of "TMC2160 DATASHEET (Rev. 1.02 / 2018-NOV-19)"
As of commit 8d505c9 one of the capacitors is C82 from E0 driver

Closed 2019-01-13.

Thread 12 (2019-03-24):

Extension Board?

akurz42, 2019-03-24:
Hey,

Just a question, not a problem: will there be a way to extend the number of steppers? Reason is that 5 drivers just don't cut it for me as I have a Triple-Extruder/Single-Nozzle setup for multi-material printing, so for me it's a minimum of 6 steppers (better 7 for separate Z-Steppers).

Cheers,
Alex

hasenbanck, 2019-03-24:
You could use the 40 pin header to connect such a board. You have access to 4 hardware PWM signals, some digital pins and the SPI bus. So you could create an extension board with aditional 4 drivers.

Please be aware that the project is currently on hiatus, since there is no real interrest by other developers for this board and I don't have the funds right now to produce development boards (It's entirely a private project).

akurz42, 2019-03-24:
Ah what a pity. A proper 32bit printer board is direly needed. The only acceptable "open" board is the RADDS, which I'm using right now. Becomes an ugly spaghetti monster when using a non-RADDS display and pulling out SPI wires to control TMCs. The Duet family is quite nice, but too restrictive for my taste.

Seems like we have to wait some more until vendors figure out that 8bit is a dead end.

Cheers,
Alex

hasenbanck, 2019-03-24:
You can't create "one fits all needs" board, so you have to pick your poison. My board RemRam is finished and commercialy available (some german shop does produce them), but has different design parameters.

There is also "ARMED", some chinese 32bit boards with Marlin support and of course Duet.

akurz42, 2019-03-24:
RemRam I know. 4x 2130 and 5V fans. 4 steppers is even further from my specs and there's no way back to 2130 after having used 5160s. Armed I don't know - that's not Re-Arm, is it?

Anyways, like you say there's no perfect solution for everyone and I realize the I'm a bit off mainstream with my requirements. Would have been nice to see another alternative in the market to set some counterweight to the Duets.

Cheers,
Alex

hansd56, 2019-12-16:
How much would it cost to get some prototype boards manufactured?

hasenbanck, 2019-12-16:
We once did a quote at a chinese board produceer. I think the price was around 250€ per unit when you let them produce 10 boards.

If you just want to build one board and buy the PCB and parts yourself, then you need to invest around 300€ and need to build it yourself.

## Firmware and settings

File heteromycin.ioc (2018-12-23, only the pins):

Mcu.UserName=STM32H743VITx
PA0.GPIO_Label=PWM_HEAT1
PA0.Signal=S_TIM2_CH1
PA1.GPIO_Label=STEP_Z
PA1.Signal=S_TIM2_CH2
PA10.Signal=USART1_RX
PA12.GPIO_Label=STATUS_LED
PA12.Signal=GPIO_Output
PA2.GPIO_Label=STEP_Y
PA2.Signal=S_TIM2_CH3
PA3.GPIO_Label=STEP_X
PA3.Signal=S_TIM2_CH4
PA4.GPIO_Label=MCU_SS
PA4.Signal=SPI1_NSS
PA5.Signal=SPI1_SCK
PA6.Signal=SPI1_MISO
PA7.Signal=SPI1_MOSI
PA9.Signal=USART1_TX
PB0.GPIO_Label=SS_Z
PB0.Signal=GPIO_Output
PB1.GPIO_Label=DIR_Y
PB1.Signal=GPIO_Output
PB10.GPIO_Label=DIR_E1
PB10.Signal=GPIO_Output
PB11.GPIO_Label=DIAG_E0
PB11.Signal=GPIO_Input
PB12.GPIO_Label=SS_E1
PB12.Signal=GPIO_Output
PB13.GPIO_Label=DIR_E0
PB13.Signal=GPIO_Output
PB14.GPIO_Label=STEP_E1
PB14.Signal=S_TIM12_CH1
PB15.GPIO_Label=STEP_E0
PB15.Signal=S_TIM12_CH2
PB2.GPIO_Label=SS_Y
PB2.Signal=GPIO_Output
PB6.Signal=I2C1_SCL
PB9.Signal=I2C1_SDA
PC0.GPIO_Label=TEMP4
PC0.Signal=ADCx_INP10
PC1.GPIO_Label=TEMP3
PC1.Signal=ADCx_INP11
PC10.Signal=USART3_TX
PC11.Signal=USART3_RX
PC2_C.GPIO_Label=TEMP2
PC2_C.Signal=ADC3_INP0
PC3_C.GPIO_Label=TEMP1
PC3_C.Signal=ADC3_INP1
PC5.GPIO_Label=DIR_Z
PC5.Signal=GPIO_Output
PC6.GPIO_Label=PWM_EXT4
PC6.Signal=S_TIM3_CH1
PC7.GPIO_Label=PWM_EXT3
PC7.Signal=S_TIM3_CH2
PC8.GPIO_Label=PWM_EXT2
PC8.Signal=S_TIM3_CH3
PC9.GPIO_Label=PWM_EXT1
PC9.Signal=S_TIM3_CH4
PD10.GPIO_Label=SS_SD
PD10.Signal=GPIO_Output
PD11.GPIO_Label=SD_DETECT
PD11.Signal=GPIO_Input
PD12.GPIO_Label=PWM_FAN1
PD12.Signal=S_TIM4_CH1
PD13.GPIO_Label=PWM_FAN2
PD13.Signal=S_TIM4_CH2
PD14.GPIO_Label=PWM_FAN3
PD14.Signal=S_TIM4_CH3
PD15.GPIO_Label=PWM_FAN4
PD15.Signal=S_TIM4_CH4
PD2.GPIO_Label=D5
PD2.Signal=GPIO_Input
PD3.GPIO_Label=D4
PD3.Signal=GPIO_Input
PD4.GPIO_Label=D3
PD4.Signal=GPIO_Input
PD5.GPIO_Label=D2
PD5.Signal=GPIO_Input
PD6.GPIO_Label=D1
PD6.Signal=GPIO_Input
PD9.GPIO_Label=SS_E0
PD9.Signal=GPIO_Output
PE10.GPIO_Label=DIAG_Y
PE10.Signal=GPIO_Input
PE11.GPIO_Label=DIAG_X
PE11.Signal=GPIO_Input
PE12.Signal=SPI4_SCK
PE13.Signal=SPI4_MISO
PE14.Signal=SPI4_MOSI
PE15.GPIO_Label=DIAG_E1
PE15.Signal=GPIO_Input
PE2.GPIO_Label=Z_MIN
PE2.Signal=GPIO_Input
PE3.GPIO_Label=Y_MIN
PE3.Signal=GPIO_Input
PE4.GPIO_Label=X_MIN
PE4.Signal=GPIO_Input
PE5.GPIO_Label=PWM_BED
PE5.Signal=S_TIM15_CH1
PE6.GPIO_Label=PWM_HEAT2
PE6.Signal=S_TIM15_CH2
PE7.GPIO_Label=DIR_X
PE7.Signal=GPIO_Output
PE8.GPIO_Label=SS_X
PE8.Signal=GPIO_Output
PE9.GPIO_Label=DIAG_Z
PE9.Signal=GPIO_Input

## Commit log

2018-10-14 Snapshot of current development
    [connectors.sch, heteromycin.kicad_pcb, heteromycin.sch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]
2018-10-16 Current snapshot
    [connectors.sch, heteromycin.kicad_pcb, heteromycin.sch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]
2018-10-16 Finished general layout and power planes
    [heteromycin.kicad_pcb, motor.sch, rpi.sch]
2018-10-17 Add SD card reader, placed temp connections, fixed stepper placement
    [connectors.sch, heteromycin.kicad_pcb, heteromycin.sch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]
2018-10-17 Fix pin layout
2018-10-18 Placed some bypass caps
    [heteromycin.kicad_pcb, motor.sch]
2018-10-19 Placed last connectors
    [connectors.sch, heteromycin.kicad_pcb, motor.sch]
2018-10-20 Some small adjustments
    [connectors.sch, heteromycin.kicad_pcb, heteromycin.sch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]
2018-10-20 First pass of routing
    [connectors.sch, heteromycin.kicad_pcb, heteromycin.sch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]
2018-10-20 Some silkscreen changes
    [heteromycin.kicad_pcb]
2018-10-21 Various changes
    * Add Status LED
    * Switched small diodes to more general available BAT54 in SOD123
    * Fixed various DRC errors
    [connectors.sch, heteromycin.kicad_pcb, heteromycin.sch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]
2018-10-21 Add i3a component
    [heteromycin.kicad_pcb, mcu.sch]
2018-10-21 Complete functional design
    [connectors.sch, heteromycin.kicad_pcb, mcu.sch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]
2018-10-21 Finish silkscreen and updated README.md
    [heteromycin.kicad_pcb, heteromycin.sch, mcu.sch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]
2018-10-21 Fix ZVD for RPi protection
    [heteromycin.kicad_pcb, rpi.sch]
2018-10-22 Change default SOT1220 MOSFET and added parts alternatives
    [heteromycin.kicad_pcb, motor.sch]
2018-10-23 Add drawings and another mounting hole
    [heteromycin.kicad_pcb, motor.sch, rpi.sch]
2018-10-23 Change mounting holes
    Pi mounting holes: M2.5
    Board mounting holes: M3
    Added a mounting hole near the board center
    [heteromycin.kicad_pcb, rpi.sch]
2018-10-23 Update image and corrected some copper pure
    [heteromycin.kicad_pcb]
2018-10-24 Add bypass cap for I2C EEPROMs and redone some copper pour
    [connectors.sch, heteromycin.kicad_pcb, mcu.sch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]
2018-10-24 Fix MOSFET selection
    [heteromycin.kicad_pcb, mosfets.sch, motor.sch]
2018-10-24 Add transistor for boot selection
    [connectors.sch, heteromycin.kicad_pcb, mcu.sch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]
2018-10-24 Move the nRESET cap a little bit
    [heteromycin.kicad_pcb]
2018-10-25 Update TXCO and STM32CubeMX configuration file
    [heteromycin.kicad_pcb, mcu.sch]
2018-10-25 Correct the name of the micro SD card reader
    [heteromycin.kicad_pcb, sdcard.sch]
2018-10-25 Change PI connector to a cheaper one
    [heteromycin.kicad_pcb, rpi.sch]
2018-10-26 Fix current sense resistor to correct value and add BOM
    [BOM-Heteromycin-v1.0.ods, motor.sch]
2018-10-26 Increase date code for v1.0 release
    [heteromycin.kicad_pcb]
2018-10-26 Increase pin tolerance for i3A DC/DC
    [heteromycin.kicad_pcb]
2018-11-10 Fix various v1.0 errors
    * Change 3.3V LDO to AP7365-33WG-7
    * Optimize soldermask clearance (from 0.2 to 0.05)
    * Connect SD connect switch to GND
    * Optimized some PADs
    [heteromycin.kicad_pcb, motor.sch, power.sch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]
2018-11-10 Add v1.1 BOM and update picture
    [BOM-Heteromycin-v1.0.ods, BOM-Heteromycin-v1.1.ods]
2018-11-10 Fixed heater output cap
    [BOM-Heteromycin-v1.1.1.ods, heteromycin.kicad_pcb]
2018-11-20 Add thermal relief to DC/DC switcher connection
    [heteromycin.kicad_pcb]
2018-11-20 Change BOM to v1.2
    02x20 connector had the wrong part number.
    [BOM-Heteromycin-v1.2.ods]
2018-11-24 Updated board to version 1.2
    * Switched small MOSFETs to SOT-23 package
    * Redesigned TMC*160 driver layout
    * Changed 01x03 to 02x03 jumper for FAN voltage selection
    * Switches STATUS_LED pin
    * Some copper pour optimizations
    [BOM-Heteromycin-v1.1.1.ods, connectors.sch, heteromycin.kicad_pcb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]
2018-11-24 Increased sense resistor value to 0.1
    This will result in a maximum 2.3A current for the stepper.
    This should act as a more sensible default. Of course the user
    can replace the sense resistors as they see fit. As long as they
    they don't stress the termal budget of the driver MOSFET that is.
    [heteromycin.kicad_pcb, motor.sch]
2018-11-24 Add silkscreen explanation for endstop pins
    [heteromycin.kicad_pcb]
2018-11-24 Connected TMC DIAG pins to MCU
    We had some pins free, so I decided to connect them, so that we
    don't need to use the ENDSTOP OVER SPI feature.
    [heteromycin.kicad_pcb, heteromycin.sch, mcu.sch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]
2018-11-24 Updated image and added some copper pour
    [heteromycin.kicad_pcb]
2018-11-25 Updated BOM for version 1.2
    [BOM-Heteromycin-v1.2.ods]
2018-12-02 Switched EEPROM I2C traces for the RPI
    SDA and SCL were switched. Also some formatting for the
    EEPROM settings.txt.
    [heteromycin.kicad_pcb, rpi.sch]
2018-12-02 Add PU for SD_DETECT_PIN
    [connectors.sch, heteromycin.kicad_pcb, motor.sch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]
2018-12-23 Update the MCU from STM32F765VI to STM32H743VI
    More speed, more RAM. Only loose the compability to flash over
    USART3. Flashing over USART1/I2C/SPI is still possible.
    [heteromycin.kicad_pcb, mcu.sch]
2019-01-11 Improve Readability
    [mcu.sch, mosfets.sch, motor.sch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]
2019-01-11 Further Improved Readability - Rotated labels
    [connectors.sch, mosfets.sch, motor.sch]
2019-01-11 Re-place some items that had broken timestamps
    [heteromycin.kicad_pcb, mcu.sch, motor.sch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]
2019-01-12 Changed boot pin drive interface
    Changed the boot pin to a direct connection since the current design depends on a existing raspberry to work. Used a 10kOhms resistor since that's the one used in the development board made by ST
    [connectors.sch, heteromycin.kicad_pcb, heteromycin.sch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]
2019-01-12 Add PD resistor to BOOT PIN
    [connectors.sch, heteromycin.kicad_pcb, heteromycin.sch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]
2019-01-12 Changed BOOT PIN PD resistor to 100kOhms
    [connectors.sch, heteromycin.kicad_pcb, heteromycin.sch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]
2019-01-12 Fix label position
    [mcu.sch]
2019-01-12 Rotated BOOT PIN resistor
    [heteromycin.kicad_pcb]
2019-01-12 Designed a layout sheet file
    [connectors.sch, heteromycin.sch, mcu.sch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]
2019-01-13 Fix BOOT PIN track
    [heteromycin.kicad_pcb]
2019-01-13 Remove old note and add notice for 100V cap on motor driver
    Anothe developer is using a RC for KiCad 6, so I need to re-
    convert and touch all files with this commit. The developer
    has been lectured and this shouldn't be necessary in the future.
    [connectors.sch, heteromycin.kicad_pcb, heteromycin.sch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]
2019-01-13 Prepare release 1.3
    * Fix LFPAK footprint (gaps)
    * Updated BOM for release 1.3
    * Updated silkscreen version number
    [BOM-Heteromycin-v1.2.ods, BOM-Heteromycin-v1.3.ods, heteromycin.kicad_pcb]
2019-01-13 Fixed wrong partnumber for TXCO
    [BOM-Heteromycin-v1.3.ods, heteromycin.kicad_pcb, mcu.sch]
2019-01-13 Fix BOM for the correct 40 PIN header
    [BOM-Heteromycin-v1.3.ods]
2019-01-13 Added LCSC Distributor to BOM
    [BOM-Heteromycin-v1.3.ods]
2019-01-13 Fix part number for 100uF cap
    [BOM-Heteromycin-v1.3.ods]
2019-01-13 Added manufacturer number to schematic
    [connectors.sch, mcu.sch, mosfets.sch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]
2019-01-13 Re anotate design
    [motor.sch]
